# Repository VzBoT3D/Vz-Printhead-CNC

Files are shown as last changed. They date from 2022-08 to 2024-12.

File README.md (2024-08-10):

# The Vz-Printhead

The Vz-Printhead is a light weight (27g full alu, and 22g hybrid carbon fiber+alu) and stiff head made for the VzBoTs, and now for Vcore3 (if using MGN9 X rail). It was designed to be compatible with almost all hotends,
and extruders out there. With the height adjustable fan duct, you can easily change your config without having to re-print a new fan duct.



## The official tool head is produced by our main partner.

 -Mellow3D 

## This project is licensed Non-commercial except for our authorized partners


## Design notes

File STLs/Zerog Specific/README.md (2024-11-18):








This duct was designed to fit with Goliath short and watercooled Vz-Hextrudort. It can also be used with other hotends, but you will need to print and scale the spacers [here](https://github.com/VzBoT3D/Vz-Printhead-CNC/blob/main/STLs/fan%20duct%20lower%20body-brace%20Z%20scalable%20spacers.stl) to mount under the printhead.

BOM:

- 4 X Heat insert M3 3mm X 4.5mm 
- M3 6mm Bolt (to mount to dancing man) 
- M3 12mm Bolt (to mount under the printhead. Or longer bolts + spacers if you use a different hotend)

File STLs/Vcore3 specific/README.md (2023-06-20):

  Please note that the fan duct Goliath short will not fit if you use the Goliath in it's short version. It will only work with Goliath when used with it's heatsink in a long format or with other hotends

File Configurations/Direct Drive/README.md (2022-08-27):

# Direct Drive has some options, and more will come later.

## Compatible extruders:

- [Vz-Hextrudort](https://github.com/VzBot3D/VzBot/tree/master/Assemblies%20BOM%20and%20STL/Vz-HextrudrORT) : Will mount from the bottom with the same holes as LGX lite
- LGX Lite 
- (Not recommended) Hextrudort  (One can decide to use the official HextrudORT version to bolt directly on the hotend without using the adapter plate. This will work but the disanvatage is that you will have to dismantle the Hextrudort everytime you will want to remove the hotend)
- Orbiter 2.0 
- Sherpa mini 
- Sherpa Micro

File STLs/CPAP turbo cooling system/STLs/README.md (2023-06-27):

for more fan duct options, check out the main STL section


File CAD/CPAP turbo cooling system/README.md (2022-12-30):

Vz-PrintHead-_CPAP1-Edit






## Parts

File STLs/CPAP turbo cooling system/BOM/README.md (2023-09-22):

| Quantity | Part | Image | comment  | Links  |
| --- | ---- | --- | -----  | -----	|
| 2 | M3 6mm bolts | M3x6_buttonhead  | To bolt cpap fan mount to alu back plate | https://s.click.aliexpress.com/e/_9RWMof |
| 2 | M3 4.6mm x 5mm heat inserts |   | to inserter in upper duct mount (for C clamp to bolt to) | [https://s.click.aliexpress.com/e/_9RWMof](https://s.click.aliexpress.com/e/_De28c87 or https://amzn.to/3ZVI5xR) |
| 3 | M2.5 screws | M4 selft tapping screw 10mm  | To screw cpap fan mount to fan | https://s.click.aliexpress.com/e/_A7Qlmx |
| 1 | cpap fan 70mm + controller | Capture7  |  | https://s.click.aliexpress.com/e/_AEsHxz or  [https://s.click.aliexpress.com/e/_AAzQAX](https://s.click.aliexpress.com/e/_AAfgBn) | |
| 1 | cpap hose 15mm ID |   |  | https://amzn.to/3zQNYSi or https://s.click.aliexpress.com/e/_A9rUYd| |

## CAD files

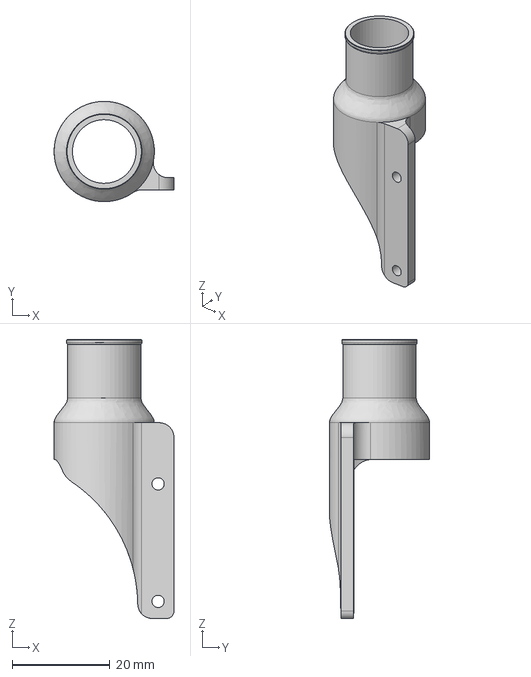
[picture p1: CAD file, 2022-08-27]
CAD/CPAP turbo cooling system/CPAP fan outlet adapter.step
24.5 x 20.5 x 57.0 mm

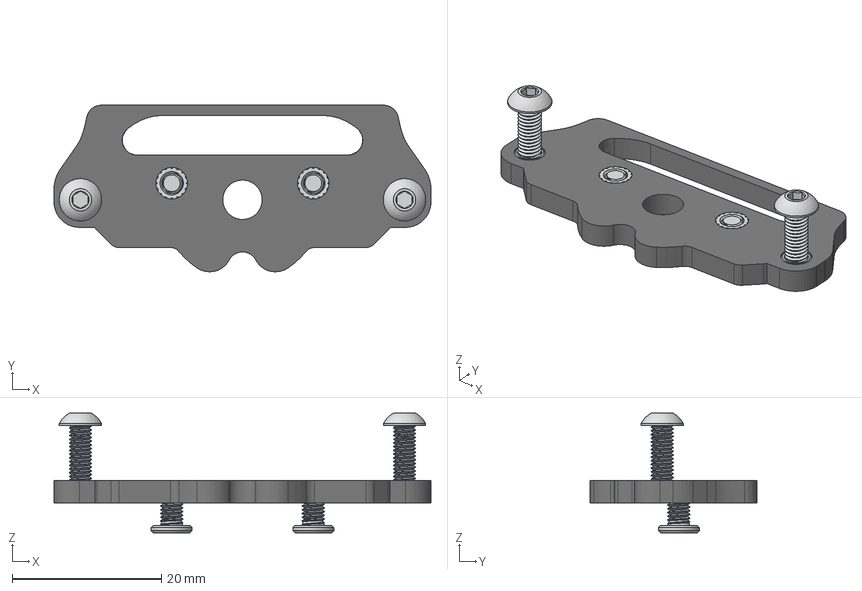
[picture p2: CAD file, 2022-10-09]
CAD/Extruder Specific/Sherpa mini adapter plate.step
50.6 x 22.4 x 16.0 mm
M3_Short x 4
M3 10mm Button Head x 2
M3 6mm Flat Head Ultra Low profile x 2

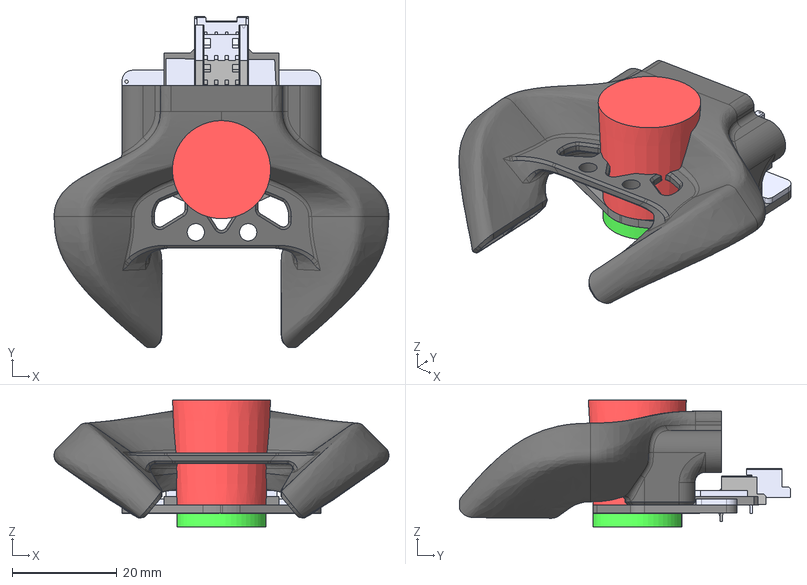
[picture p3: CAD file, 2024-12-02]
CAD/Vz-PrintHead/Fan Ducts and +/Goliath short fan duct Beacon.step
64.0 x 63.3 x 24.2 mm
Beacon_RevH_Assm_LowProfile

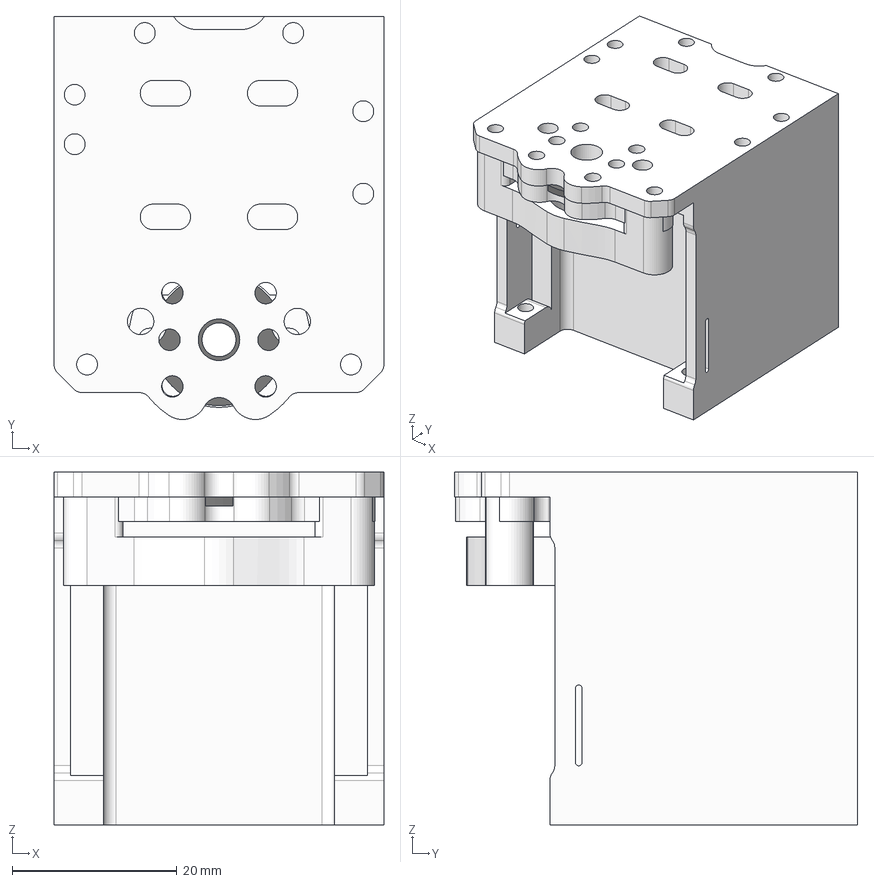
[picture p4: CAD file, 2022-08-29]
CAD/Vz-PrintHead/Vcore3/Vz-PrintHead Vcore3.step
40.0 x 48.9 x 42.8 mm
Hotend adapter plate
LGX-Dragon/Rapido-Nova adapter
1.1mm printed spacer

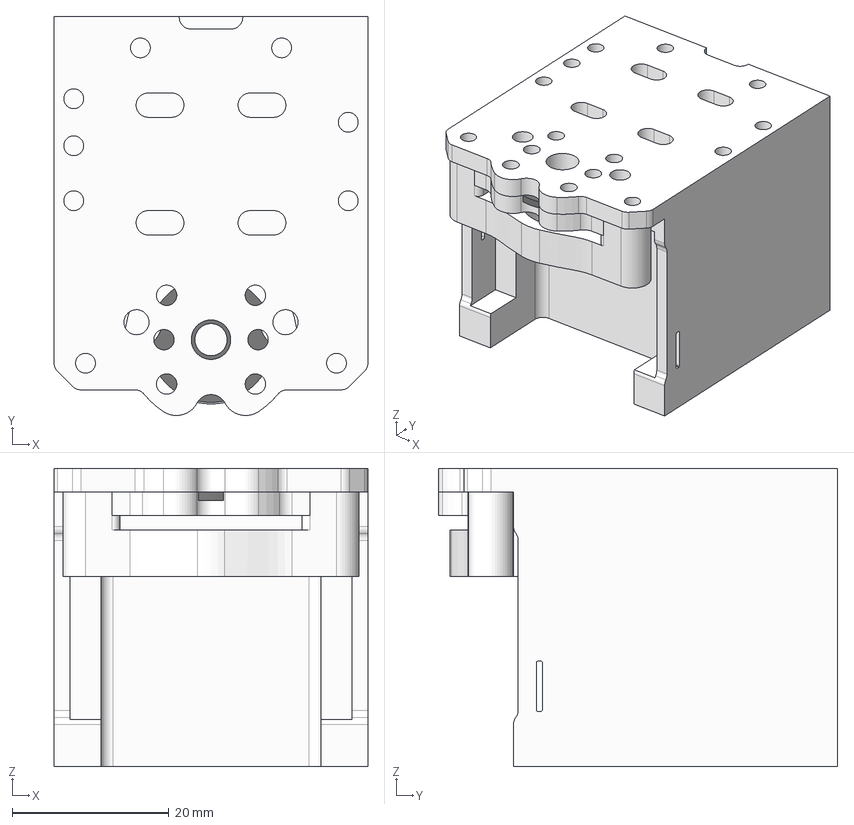
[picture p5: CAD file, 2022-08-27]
CAD/Vz-PrintHead/VzBoT/Vz-Printhead VzBoT.step
40.0 x 50.9 x 38.0 mm
Hotend adapter
1.1mm printed spacer
Print head

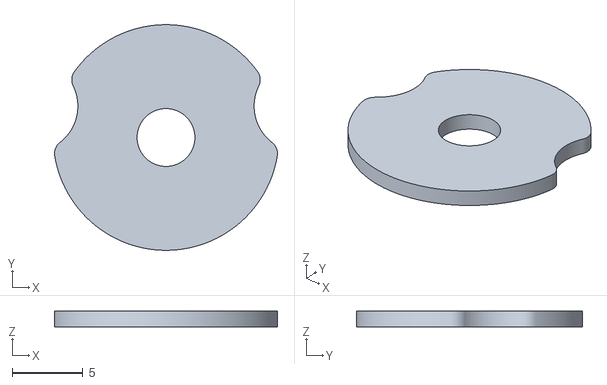
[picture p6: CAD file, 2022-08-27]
Configurations/BOWDEN/GrooveMount/STLs/Groove mount 1.1mm spacer.stl
15.8 x 16.0 x 1.10

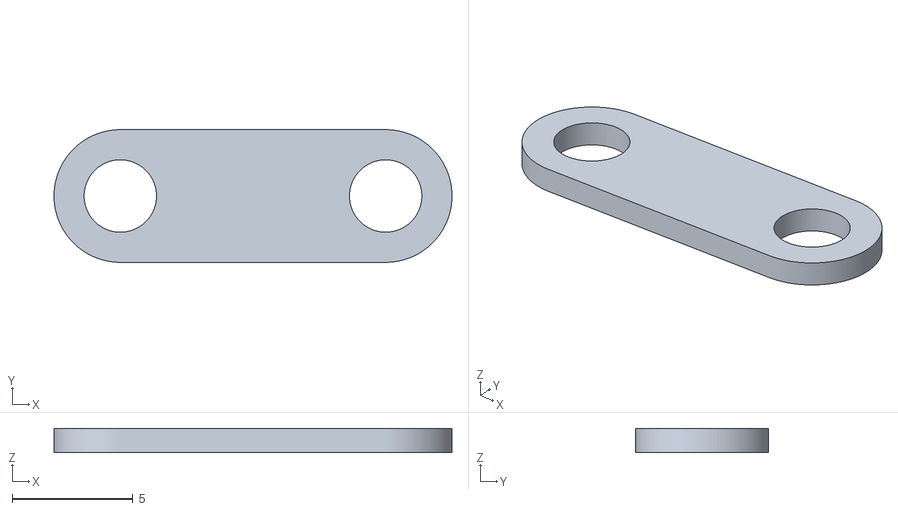
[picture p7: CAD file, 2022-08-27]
Configurations/BOWDEN/Mosquito Magnum+/STLs/magnum brace-stancil.stl
16.5 x 5.50 x 1.00

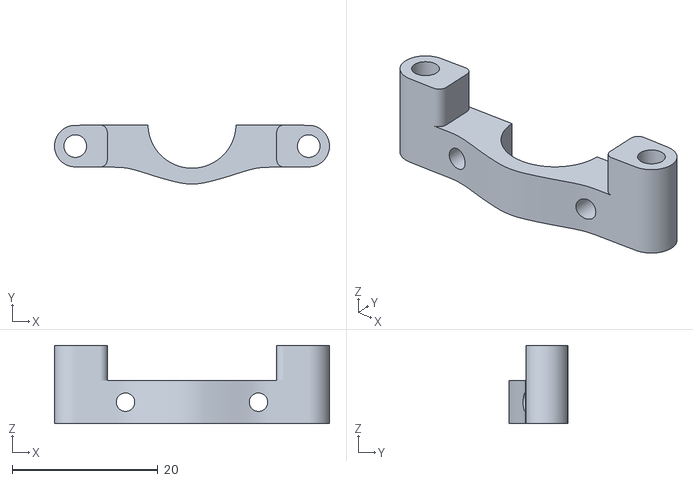
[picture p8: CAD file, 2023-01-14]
Configurations/Direct Drive/Hotends config/GrooveMount/STLs/GroveMount adapter1.stl
37.7 x 8.10 x 10.8

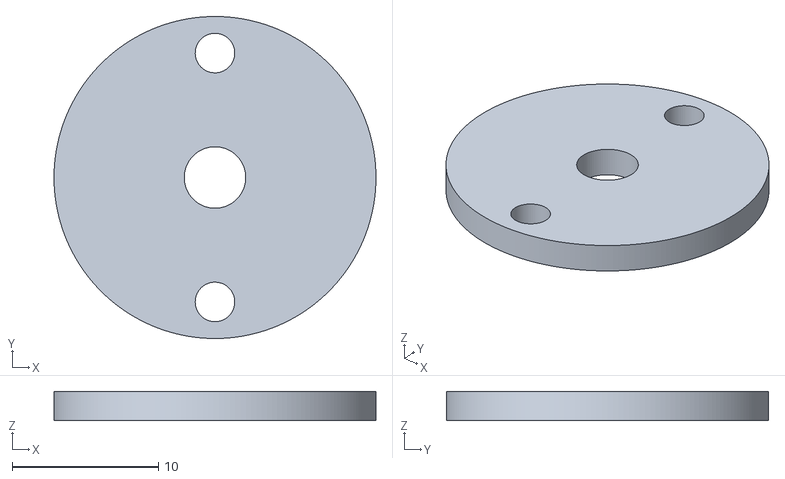
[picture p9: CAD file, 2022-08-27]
Configurations/Direct Drive/Hotends config/Nova HotEnd/STLs/Nova 2mm spacer.stl
22.0 x 22.0 x 2.00

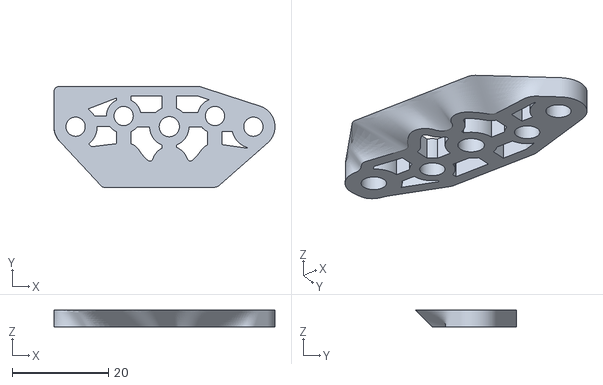
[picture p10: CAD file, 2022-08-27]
Configurations/Direct Drive/Orbiter/STLs/Adapter plate with inserts.stl
46.0 x 21.0 x 3.50

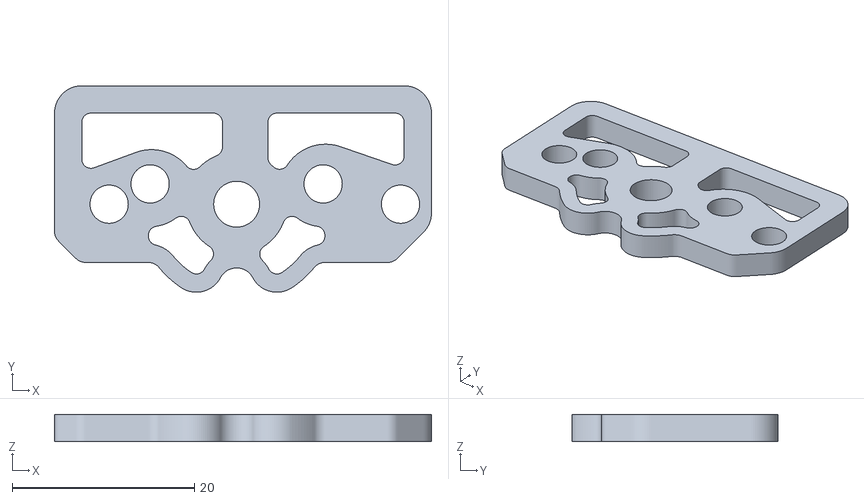
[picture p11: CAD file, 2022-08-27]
Configurations/Direct Drive/Sherpa Micro/STLs/Sherpa micro adapter plate with inserts.stl
41.4 x 22.7 x 3.00

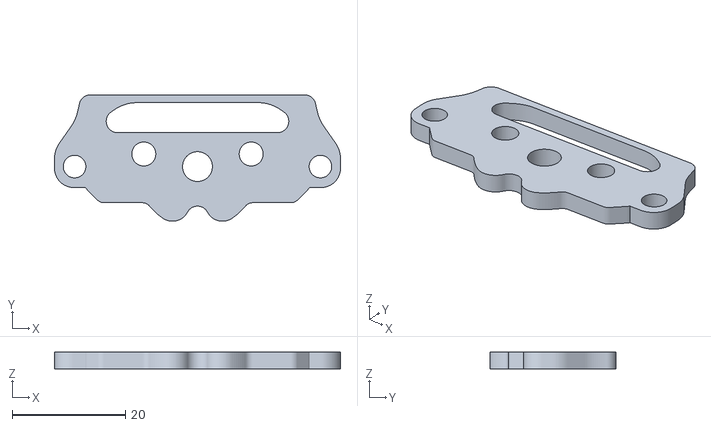
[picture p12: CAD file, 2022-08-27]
Configurations/Direct Drive/Sherpa Mini/STLs/Sherpa mini adapter plate with inserts.stl
50.6 x 22.4 x 3.00

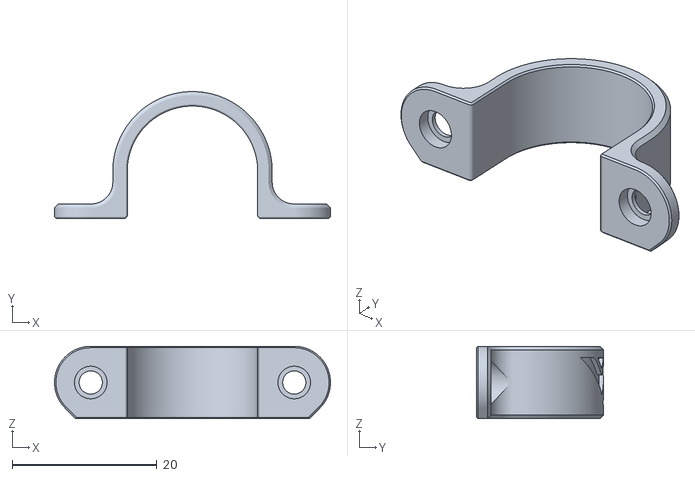
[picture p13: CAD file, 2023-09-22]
STLs/CPAP turbo cooling system/STLs/c-clamp.stl
38.1 x 17.5 x 10.0

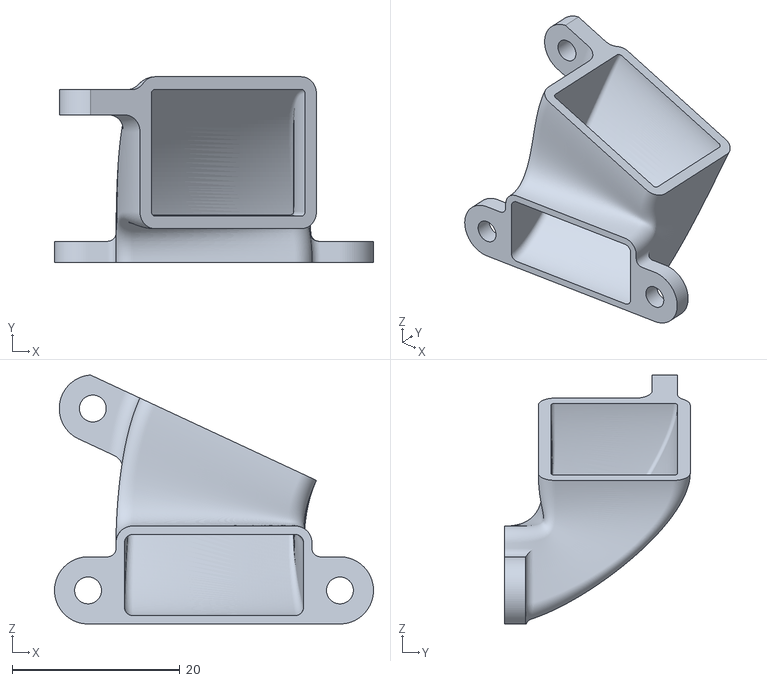
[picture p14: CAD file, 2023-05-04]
STLs/fan duct upper body 5015-beacon.stl
38.0 x 22.1 x 29.7

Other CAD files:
STLs/hevort specific/Belt Clip 9mm.stl
STLs/Probe mounts/Beacon/Upper duct 5015.stl
CAD/CPAP turbo cooling system/CPAP fan mount.step
CAD/Extruder Specific/Orbiter v2-adapter plate.step
CAD/Extruder Specific/SherpaMicro adapter plate.step
CAD/Vz-PrintHead/Fan Ducts and +/Dragon 2510 fan duct non-vcore3.step
CAD/Vz-PrintHead/Fan Ducts and +/Goliath short fan duct.step
CAD/Vz-PrintHead/Fan Ducts and +/trihorn Fan Duct w-brace.step
Configurations/Direct Drive/Hotends config/GrooveMount/STLs/GroveMount adapter2.stl
Configurations/Direct Drive/Orbiter/STLs/Adapter plate wo inserts.stl
STLs/Belt_clip.stl
STLs/CPAP turbo cooling system/STLs/CPAP 24v board mount.stl
STLs/CPAP turbo cooling system/STLs/CPAP fan mount.stl
STLs/CPAP turbo cooling system/STLs/CPAP fan outlet adapter.stl
STLs/CPAP turbo cooling system/STLs/upper duct mount.stl
STLs/Dragon 2510 Fan Shroud w brace for VzBoT only.stl
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

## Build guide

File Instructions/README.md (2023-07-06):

Assembling the print head is straight forward.

# Step 1 : Mounting the Fan and Cable holder.

## BOM needed:
- 4xM3 6mm Ultra low profile bolts or button head (Button head should allow more tolerance between 2 bolt heads)
- cable holder (printed)
- Loctite the 2 bolts that secures it to the main carriage

# Step 2 : Assembling the carriage
- Install the top plate on the X MGN9 slider
- Install the back, front, and bottom plates


## BOM needed:
- 12xM3 6mm Ultra low profile bolts (For all 8 corners and MGN9 bloc). For F3D printhead
- For Mellow kit, it needs 4x5mm or 4x4mm bolts for the MGN9 bloc. Kit should include M3 4mm.

# Step 3: Mounting the the X stop switch (Optional: if you don't use sensorless homing)

### Rat Rig Vcore3 users: You will need to add this X stopper to your Left Xy joiner. STL found [here](https://github.com/VzBoT3D/Vz-Printhead/blob/main/STLs/Vcore3%20specific/Vcore3_X_stopper.stl) 
Please note that you will need a 15mm M5 bolt instead of a 12mm


Also, you can re-use the Vcore original X switch with this [mount](https://github.com/VzBoT3D/Vz-Printhead/blob/main/STLs/Vcore3%20specific/X-endstop-mount.stl)

## BOM needed:
- 2 x M3 6mm Ultra low profile bolts
- 2 x M2 screws (not included in the kit)
- Microswitch https://s.click.aliexpress.com/e/_AL9anj
- Switch mount (Printed)

# Step 4: Install the rear adjustable fan mount

## BOM needed:
- 2 x M3 8mm Ultra low profile bolts (or 2x6mm for the new version of the mount that has a groove for the M3 nuts)
- 2 x M3 Nuts

# Step 5: Install the belts.
- make sure motor mounts are a lowest tension possible first.
- Start by the front. Insert the end of the belt through the side slot and loop the belt on itself. Insert a piece of filament (6mm) in the loop and then slowly pull the belt back in the slot until secures in place.
- For the back, simply loop the belt arround the pillar, and give it a pre-tention on the belt, then attach it with a zip tie, or a printed belt clip (Found in the [STL](https://github.com/VzBoT3D/Vz-Printhead/tree/main/STLs) folder) . [belt clip](https://github.com/VzBoT3D/Vz-Printhead/blob/main/STLs/Belt_clip.stl)
- [belts-installation)](https://youtu.be/Ibi27Toh-pg)
- (For Vz235, you can use 2 techniques described here in this [video](https://www.youtube.com/watch?v=lP59PClF_PU&t=3334s). For the optional 2 piece clips, here they [are](https://github.com/VzBoT3D/VzBoT-Vz235/tree/main/Assemblies%20%26%20STL/Gantry/Misc))
- Vz235: - 

# Step 5.1
Take a rum shot. This step is definately needed after the belts job. It takes a bit of patience to route the belts in the front idlers, with a small screw driver, its very doable

# Step 6: Install the fan duct

## BOM needed:
- 2 x M3 10mm bolts
- 2 x M3 Nuts
- Upper fan duct (printed)
- Lower fan fuct (printed)

# Step 7: Install your favorite extruder/hotend combo.
Refer to the "Configuration" sections above (or links down below)for instructions and BOM
- [BOWDEN](https://github.com/VzBoT3D/Vz-Printhead/tree/main/Configurations/BOWDEN)
- [Direct Drive](https://github.com/VzBoT3D/Vz-Printhead/tree/main/Configurations/Direct%20Drive)

# Step 7.1
Take a second well deserved rum shot. Please note that beer can be used in this step.

# Step 8 : Adjust the fan height
Loosen the 2 M3 8mm bolts, and ajust height according to your Hotend


# Step 9 : Install the 5015 fan  (BL touch is not recommended anymore on VzBoT)


## BOM needed:
- 1 x M3 20mm bolt - (For right side of the fan when you face printer )
- 1 x M3 25mm bolt - (for left side  Please note the left side bolt orientation is different to clear the belt)
- 1 M3 8mm (upper fan duct brace)
- 3 x M3 Nuts

# Optional : Tri horn fan duct with brace (useful when running a z probe sensor)
If you find that your fan duct is not stiff enough and move after a while, this mod of the fan [duct](https://github.com/VzBoT3D/Vz-Printhead/blob/main/STLs/fan%20duct%20lower%20body-trihorn%20with%20brace.stl) is for you. Scale the [spacers](https://github.com/VzBoT3D/Vz-Printhead/blob/main/STLs/fan%20duct%20lower%20body-brace%20Z%20scalable%20spacers.stl) according the the height needed.

(If you wish to run CPAP, refer to the CPAP section)

# Optional : Rear pillar brace
If you do not need to bring the fan all the way down, you can print and install this little [BRACE](https://github.com/VzBoT3D/Vz-Printhead/blob/main/STLs/Rear%20pillar%20brace.stl) that will help secure the cable mount in place


# Optional : PROBE  see all options [here](https://github.com/VzBoT3D/Vz-Printhead-CNC/tree/main/STLs/Probe%20mounts)

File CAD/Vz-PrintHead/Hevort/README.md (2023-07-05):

WEB viewer: https://a360.co/413Azke



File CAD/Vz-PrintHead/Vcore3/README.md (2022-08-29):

Mockup CAD of the Vocre3 printhead. Please note this is not the VzBoT version.



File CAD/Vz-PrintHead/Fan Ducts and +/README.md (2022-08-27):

The Vz-PrintHead fan duct is based on the EVA 2.3 and earlier release. It was modified to fit the VzPrintHead. The rear duct is shorter in length to fit the size of the smaller Vz-head.
Also, the under duct has been slightly modified to allow the duct to go higher witout hitting the bottom plate of the carriage. That way, we can fit shorter hotend like Nova, Mosquito and others








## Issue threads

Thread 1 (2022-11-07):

RatRig Version Questions

nicedevil007, 2022-11-07:
Hey Vez,

a few Questions here that would be nice answered in this repo on the docu page :)

I have a Ratrig and I'm getting a Printhead (right version) in a few weeks. So here are the questions:

- is everything from here compatible with the RatRig version? F.e. Rapido UHF Fanduct
- is the CPAP turbo cooling system all possible with the RatRig version?
- how to tighten the belts on a RatRig without the ability of the moving motors as you have on the VzBot (are you planning on adding anything to the RatRig community as well or does this belong to the community of RatRigs to create anything similar?)

Maybe a quick feature request that not only belongs to RatRig Version:

- Would it be possible to add a Fanduct for the Papst RLF 35-8/14 N => https://www.ebmpapst.com/ch/de/produkte/radialventilatoren/p/RLF35814N.html
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

StepFile: [RLF35814N-981727.zip](https://github.com/VzBoT3D/Vz-Printhead/files/9955308/RLF35814N-981727.zip)

Closed 2025-01-02.

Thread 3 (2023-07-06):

Add missing screw holes

ZyberSE, 2023-07-06:
It would be really great if the missing screw holes could be added, especially those on the bottom edges.
And if possible also add the screws so parts can easily be designed to sit on-top of them.

Closed 2025-01-02.

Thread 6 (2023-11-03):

Mellow sells printhead, link missing in readme

HumbleDeer, 2023-11-03:
Regarding: https://github.com/VzBoT3D/Vz-Printhead-CNC/tree/main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

This states the Vz-Printhead-CNC is produced by two main partners, both with mutually exclusive markets.

As far as I know, Mellow *does* sell the Vz-Printhead-CNC outside of Asia through their AliExpress page? https://www.aliexpress.com/item/1005005738653240.html

Closed 2025-01-02.

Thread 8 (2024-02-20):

Fan Duct Modifications to Support Beacon RevH

TheAZtech, 2024-02-20:
Beacon RevH is now an all in one design as the the silicone has been moved forward and the current duct design does not allow the Beacon to be mounted property.

I am requesting to have the fan ducts that support Beacon modified to accept the new RevH design.

Link to the STEP for the RevH: https://github.com/beacon3d/docs/blob/master/mcad/beacon/Beacon_RevH_Assm_LowProfile.STEP

Thank you for your great work and time!

EDIT: Grammer

pbsuper, 2024-12-02:
The ducts should be updated now and no longer hit the chip.

Closed 2024-12-02.

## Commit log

2022-08-27 Adding CAD
    [8mm_probe_adapter option1.stl, 8mm_probe_adapter option2 part1.stl, 8mm_probe_adapter option2 part2.stl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]
2022-08-27 adding pics
    [Adapter plate with inserts.stl, Adapter plate wo inserts.stl, Groove mount 1.1mm spacer.stl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]
2022-08-29 adding Vcore3 Cad
    [Vz-Printhead VzBoT.step]
2022-08-29 Create Vz-PrintHead Vcore3.step
    [Vz-PrintHead Vcore3.step]
2022-08-29 Create LSD Mockup AIR.step
    [LSD Mockup AIR.step]
2022-08-30 Create LSD Mockup Water.step
    [LSD Mockup Water.step]
2022-09-11 Create Dragon 2510 fan duct.step
    [Dragon 2510 fan duct.step]
2022-10-01 Create Dragon 2510 Fan Shroud wo brace.stl
    [Dragon 2510 Fan Shroud wo brace.stl]
2022-10-01 Adding Dragon std 2150 fan duct
    [Dragon 2510 Fan Shroud w brace for VzBoT only.stl]
2022-10-09 Added CAD for extruder Adapter plates
    Sherpa micro, Sherpa Mini, Orbiter v2
    [Orbiter v2-adapter plate.step, Sherpa mini adapter plate.step, SherpaMicro adapter plate.step]
2022-10-14 Create trihorn Fan Duct w-brace.step
    [trihorn Fan Duct w-brace.step]
2022-12-09 Update Dragon 2510 Fan Shroud wo brace.stl
    [Dragon 2510 Fan Shroud wo brace.stl]
2022-12-29 minor update to fan duct Goliath
    [fan duct lower LSD spacers.stl]
2022-12-30 Create Goliath lower Titanium brace template.stl
    [Goliath lower Titanium brace template.stl]
2022-12-30 changed LSD to Goliath name
    [fan duct lower Goliath spacers.stl]
2023-01-03 Create Rapido 2510 Fan Shroud wo brace.stl
    [Rapido 2510 Fan Shroud wo brace.stl]
2023-01-03 move fan shroud to vcore
    [Rapido 2510 Fan Shroud wo brace.stl]
2023-01-14 adding STL for groove mount
    since this part is not very popular, we don't mass produce it and may be out of stock. So adding Printed option in case
    [GroveMount adapter1.stl, GroveMount adapter2.stl]
2023-01-16 Create Rear pillar brace.stl
    [Rear pillar brace.stl]
2023-01-23 Create Rapido 2510 Fan Shroud with flange.stl
    [Rapido 2510 Fan Shroud with flange.stl]
2023-01-24 adding printable grove mount
    [GroveMount adapter1.stl, GroveMount adapter2.stl]
2023-01-25 moved Grove mount adapter STL in the good section
    [GroveMount adapter1.stl, GroveMount adapter2.stl]
2023-01-31 Create fan duct lower Goliath option2.stl
2023-02-04 Create fan duct lower Goliath option2 with Beacon.stl
2023-02-04 Adding CAD for the new Goliath short (option2) fan duct
    [Goliath fan duct option2 Beacon.step, Goliath fan duct option2.step]
2023-02-09 adding 8mm probe mount + fan duct Goliath for Vcore3
    [8mm_probe_adapter option3.stl, Goliath fan duct brace scalable.stl]
2023-02-09 removing old probe mount
    [8mm_probe_adapter option1.stl, 8mm_probe_adapter option2 part1.stl, 8mm_probe_adapter option2 part2.stl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]
2023-02-09 folder structure for probes
    [8mm_probe_adapter.stl, BLtouch mount.stl]
2023-02-09 Create fan duct Goliath scalable brace.stl
    [fan duct Goliath scalable brace.stl]
2023-02-20 Adding QD1 and QD2 probe option
    [probe.stl]
2023-02-20 Create Dual horn QD2.stl
2023-02-20 Create Goliath long QD2.stl
2023-02-20 rename QD probe holder
    [probe holder.stl]
2023-02-21 adding fan duct cad
    [Goliath fan duct option2 Beacon.step, Goliath fan duct option2.step, Goliath short fan duct Beacon.step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]
2023-02-25 fixed STL.
2023-03-16 adding beacon fan duck mount
2023-03-20 Adding 5015 new upper duct that fits beacon
    [Upper duct 5015.stl]
2023-05-02 Adding Tentacool and Trihorn fan duct for RatRig
2023-05-04 adding 5015 upper duct to fit beacon
    [fan duct upper body 5015-beacon.stl, fan duct upper body 5015.stl]
2023-06-27 Adding Hevort cad and STLs
    [LSD Mockup AIR.step, LSD Mockup Water.step, X optical stop switch mount.stl]
2023-06-27 Adding Hevort Belt clips
    [Belt Clip 12mm.stl, Belt Clip 9mm.stl]
2023-09-22 update to CPAP tube rear mount
    CPAP STLs also have been re-exported to have the correct print-orientation
    [CPAP 24v board mount.stl, CPAP fan mount.stl, CPAP fan outlet adapter.stl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]
2023-10-24 Adding Beacon support for Vcore3
    Tentacool with beacon support
    -New fan duct and new rear CPAP tube duct for Beacon
2023-10-27 adding tentacool duct cad
2023-12-21 Updated holes in Beacon mount to M3 size.
2024-04-17 Update Goliath short with Beacon.stl
    Update to fit all models including model H
2024-06-12 added spacers and hole updating.
    Hole for Spacer from 2.5mm to 2.85mm for easier use with m3 bolts.
    [fan duct lower Goliath spacers.stl]
2024-12-02 added Zerog fan duct
    -Added zero fan duct for beacon, to use longer hotend (goliath long etc).
    [Zerog VZ Belt Clip v1.stl, Zerog VZ Belt Clip.step, fan duct 3.5mm spacer.stl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]
2024-12-02 Update fan duct lower Goliath short with Beacon.stl
    Goliath short fan duct now ok with beacon H
2024-12-02 Update Goliath short fan duct Beacon.step
    [Goliath short fan duct Beacon.step]
2024-12-02 Goliath short fan duct updated
    Fits Beacon H + correction to the holes for the spacers for M3 (now 3.3mm ID)
    [Goliath short fan duct Beacon.step]
2024-12-06 fan duct beacon probe updated
    Removed the outdated version of the .stl file and clarified the instructions for better understanding.
    [fan duct lower Goliath spacers.stl]
2025-01-02 Rename fan duct lower Goliath short with Beacon.stl to Goliath short with Beacon
    renamed
2025-01-02 Update and rename Goliath short with Beacon to Goliath short with Beacon.stl
    [Goliath short with Beacon.stl]
2025-01-03 Revert "fan duct beacon probe updated"
    This reverts commit af33bb8e9d5b21c2333216a7f013050b940bee4c.
    [fan duct lower Goliath spacers.stl]
